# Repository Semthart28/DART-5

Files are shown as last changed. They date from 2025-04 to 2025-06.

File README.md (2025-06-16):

# Upgrading DART: Adding Traffic Light Detection and Control

<p align="center">
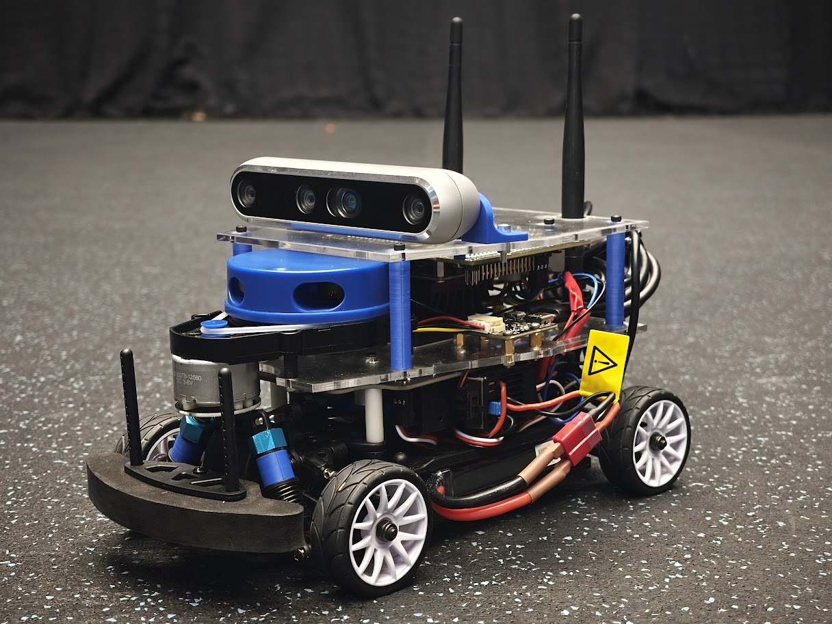
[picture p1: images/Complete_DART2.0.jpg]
  
</p>

# This Repo
In this repository, we're upgrading the DART robot for traffic light detection. DART is a robot, created at the TU Delft, and instructions for building your own DART can be found [here](https://github.com/Lorenzo-Lyons/DART). In this repository, you'll find:
+ <b>Build instructions</b> for physical changes we made.
+ <b>Build instructions</b> for our 3D-printed traffic light.
+ <b>Software for Traffic Light Detection</b> in order that the DART recognises a traffic light and which light it's currently displaying.
+ <b>Control</b> a control algorithm that makes sure the DART stops for a red light, continues through a green light, and acts appropriately to a yellow light.

# Physical Changes We Made to DART
The physical changes we made to the DART:
+ We changed the baseboard and upperboard to lower the center of mass as much as possible, mount the electronics better, and be able to install the new camera setup and LiDar power supply.
+ We connected the LiDAR's power supply directly to the Jetson Nano Expansion Board rather than to the Jetson Nano itself. This setup resolves the issue of the LiDAR drawing too much current from the Jetson Nano.
+ We added a new camera setup to enable the DART to perform traffic light detection.
+ We 3D-printed spacers to stiffen the suspension. (Originally, brass spacers were installed.)

To see the full Build Instructions for these changes, and how to replicate our 3D-printed traffic light, go to [Build Instruction Section](https://github.com/Semthart28/DART-5/tree/main/Build%20Instructions).

# Software for Traffic Light Detection
For the traffic light detection, we trained the YOLOv3-tiny model on roughly 500 images of our 3D-printed traffic light. [YOLO](https://pjreddie.com/darknet/yolo/) 'You Only Look Once' is  an open-source, state-of-the-art real-time object detection system [1]. A short clip of the detection of a traffic light is shown below:

<p align="center">
  Demo of feature
</p>

We drew the bounding boxes around the traffic light with [LabelImg](https://github.com/HumanSignal/labelImg) to create the .txt files that tell the model which class it is (0, 1, or 2 for Red, Yellow, or Green, respectively) and the coordinates that define the bounding box around the traffic light. We then used an 80/20 training/testing split with the images.

Our configuration file is based on [Berktepebag's Github](https://github.com/berktepebag/Traffic-light-detection-with-YOLOv3-BOSCH-traffic-light-dataset) with these changed settings for the training:
+ We set the max iterations to 6000 
+ We set the batch to 64
+ We set the subdivision to 12
+ We set the steps to 4800, 5400

The DART can detect the traffic light colors from more than 1.5 meters away. Below are the instructions to add the traffic light detection to your DART.

### Step 0: Setting up the camera
To set up the camera on the Jetson Nano, run this command:
```
sudo apt-get install ros-$ROS_DISTRO-realsense2-camera
```

### Step 1: Installing Darknet
Darknet from the [original website](https://pjreddie.com/darknet/) is pretty outdated. However, so is the Jetson Nano, so it'll work fine. If you're on your laptop and trying yolo, we recommend installing Darknet via [AlexeyAB's Github](https://github.com/AlexeyAB/darknet), because you're going to run into compatibility issues. But on the Jetson Nano, you should install it from the original website like this:
```
git clone https://github.com/pjreddie/darknet.git
cd darknet
make
```
Now, make sure you've downloaded CUDA and OpenCV. The Jetson Nano already has CUDA pre-installed if you downloaded the Jetpack SDK. In the Makefile in the Darknet directory, edit the lines at the top like this:
```
GPU=1
OPENCV=1
```
Remake Darknet and you're done.

### Step 2: Download our Trained Model
In your Darknet directory, make a folder called 'Model' and add the three files from [this folder](https://github.com/Semthart28/DART-5/tree/main/YOLO-model). Then, make a folder called 'backup' within the 'Model' folder and add the 'yolov3-tiny-tf_best.weights' file in there.

### Step 3: Running the model
Make sure you're in the darknet directory and run this command to run the model:
```
./darknet detector demo Model/tf-data.data Model/yolov3-tiny-tf.cfg Model/backup/yolov3-tiny-tf_best.weights
```
A tab of your camera should now open, and the algorithm will detect traffic lights!

Additionally, you can play around with the threshold of when it will show the traffic light. Just add this at the end of the previous command:

```
-thresh 0.20
```

Now, it detects all traffic lights if the confidence is higher than 20%.

# Control Algorithm 
The first thing we need to do now is to turn our detection algorithm into a ROS package so the DART can act upon this information. This is done via the [darknet_ros Github](https://github.com/leggedrobotics/darknet_ros). Follow the melodic-and-noetic branch, but download the YoloObjectDetector.cpp file from this repository. We made the .cpp file compatible with the DART by using the fix/memory_leak branch. Originally, the RAM would fill up, and the system would freeze. Additionally, we made sure the color codes of Darknet ROS and the Intel camera match up. 

Next up, download the tf_controller_pkg folder from this repository, and put it in your catkin workspace. Remake your catkin workspace and run it with this command:

```
roslaunch tf_controller_pkg tf_controller.launch
```

The safety value is still on, so you have to run the gamepad basic file and hold R1 on the controller to remove the safety value. Comment out all the throttle commands in the gamepad_basic.py file from [Lorenzo's GitHub](https://github.com/Lorenzo-Lyons/DART), and put the throttle value in the racecar_universal.py file to 0.13. Run these in separate terminals:

```
rosrun racecar_pkg racecar_universal.py
```

```
rosrun racecar_pkg gamepad_basic.py
```

Now hold the R1 button on the controller to disable the safety value and the control works!

# References
https://github.com/Lorenzo-Lyons/DART

https://pjreddie.com/darknet/yolo/

https://github.com/berktepebag/Traffic-light-detection-with-YOLOv3-BOSCH-traffic-light-dataset

https://github.com/HumanSignal/labelImg

https://github.com/AlexeyAB/darknet

https://github.com/leggedrobotics/darknet_ros

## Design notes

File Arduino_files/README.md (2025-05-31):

# Arduino Traffic light file
You'll find the Arduino code to power the traffic light and control its lights here. You can change the duration, brightness and order of the lights in this file as you like. For example, during testing you can comment out the code that displays the green and orange light to test whether the DART stops for red.

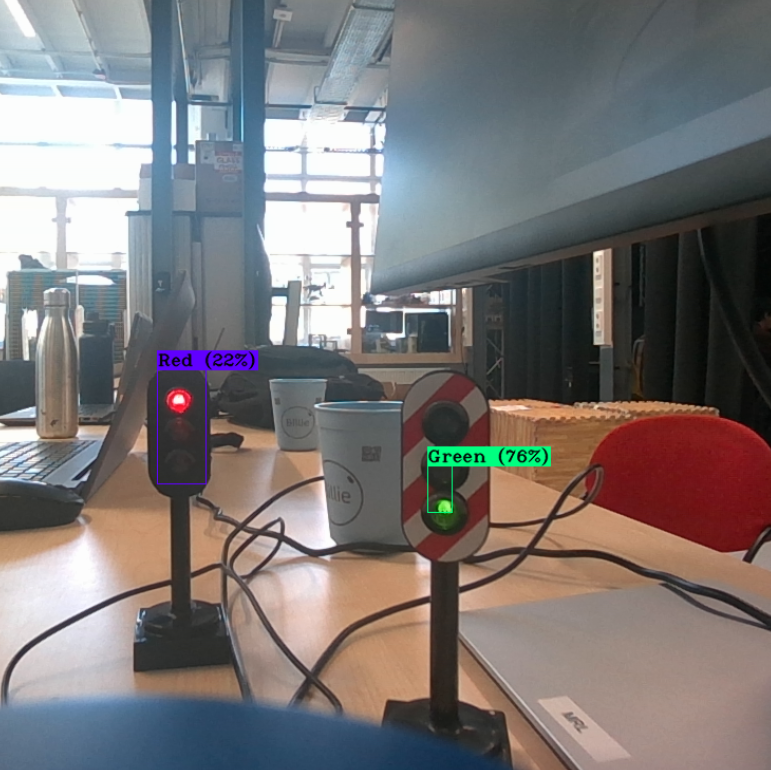
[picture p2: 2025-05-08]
images/Detection.png

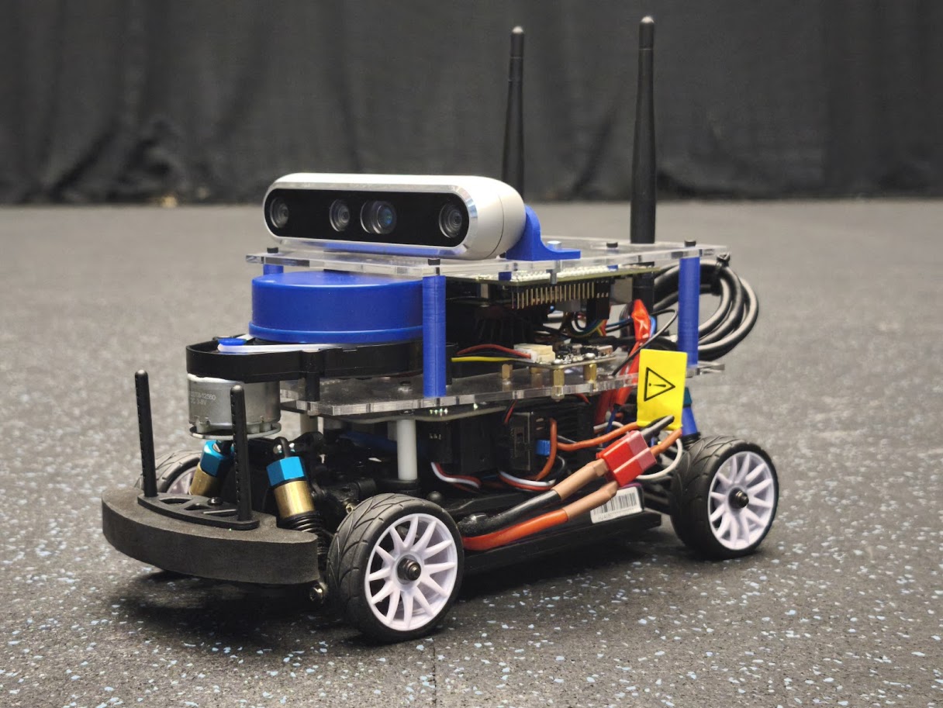
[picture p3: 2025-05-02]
images/Complete_DART.jpg

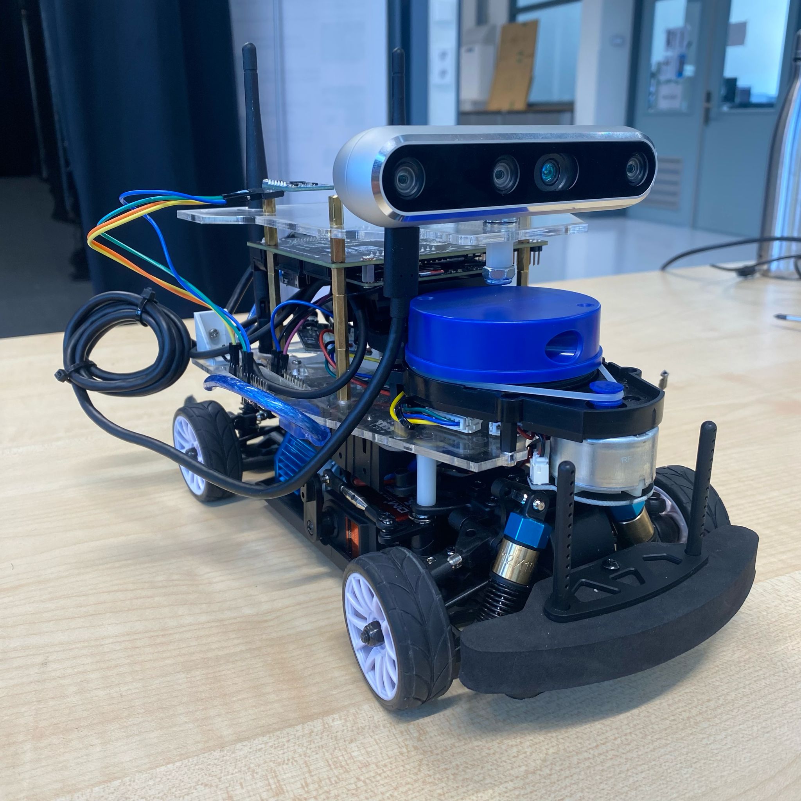
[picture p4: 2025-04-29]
images/DART.jpg

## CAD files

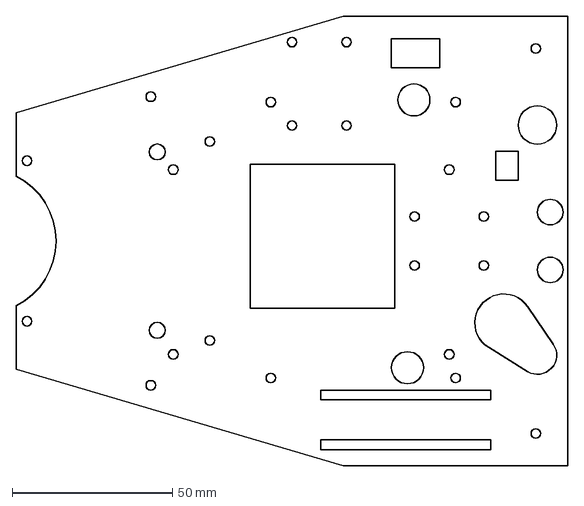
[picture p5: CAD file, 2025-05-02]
Build Instructions/DXF files/PMMA_3mm_1x_baseboard.DXF
172.0 x 140.0 mm

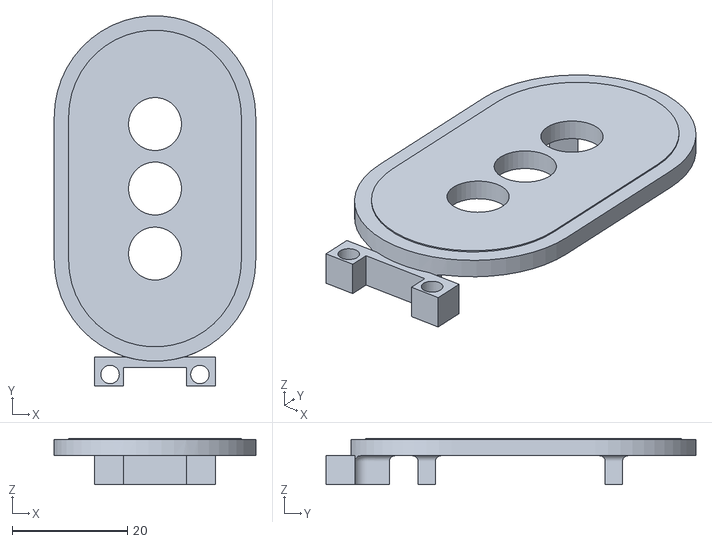
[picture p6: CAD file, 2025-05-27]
Build Instructions/STL files/Traffic light front.STL
35.0 x 64.3 x 8.00

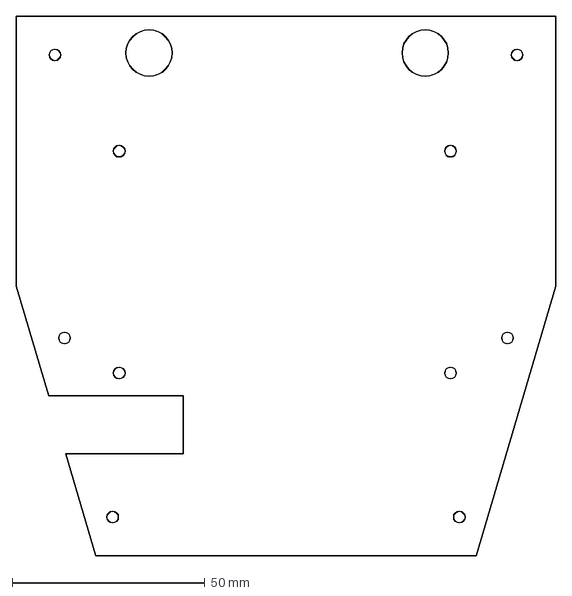
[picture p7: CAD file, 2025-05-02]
Build Instructions/DXF files/PMMA_3mm_1x_topboard.DXF
140.0 x 140.0 mm

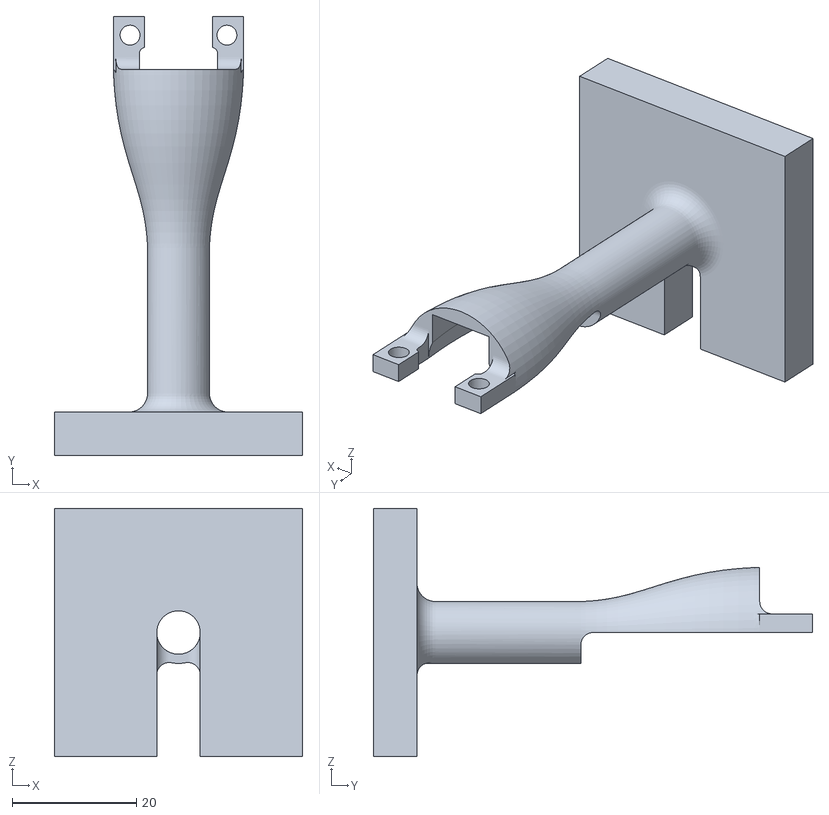
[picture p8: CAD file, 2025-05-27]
Build Instructions/STL files/Traffic light pole.STL
40.0 x 70.7 x 40.0

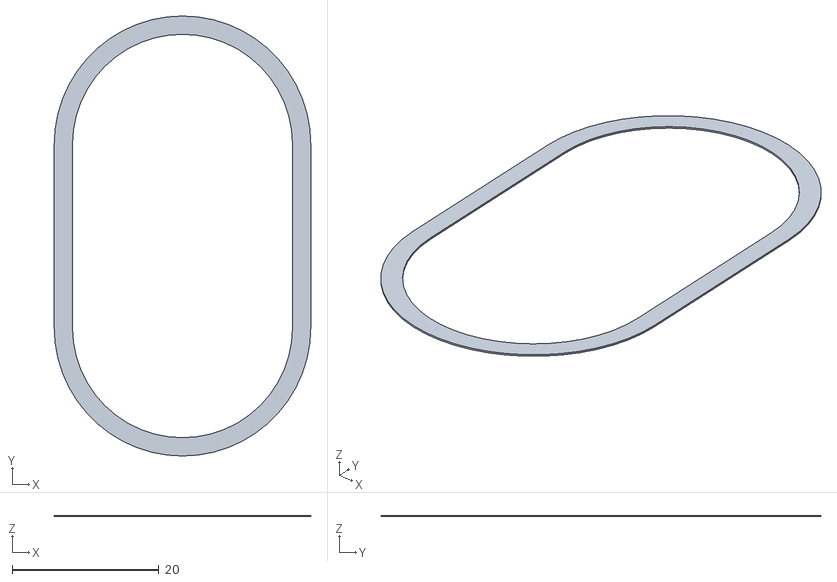
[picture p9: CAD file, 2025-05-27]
Build Instructions/STL files/Traffic light white outer line.STL
35.0 x 60.0 x 0.2

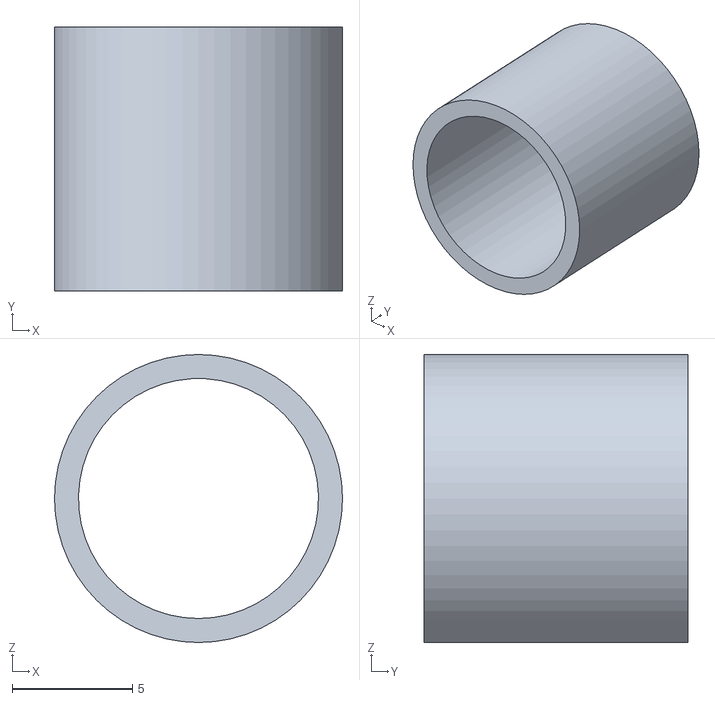
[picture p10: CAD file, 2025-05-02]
Build Instructions/STL files/Bus 12x11.STL
12.0 x 11.0 x 12.0

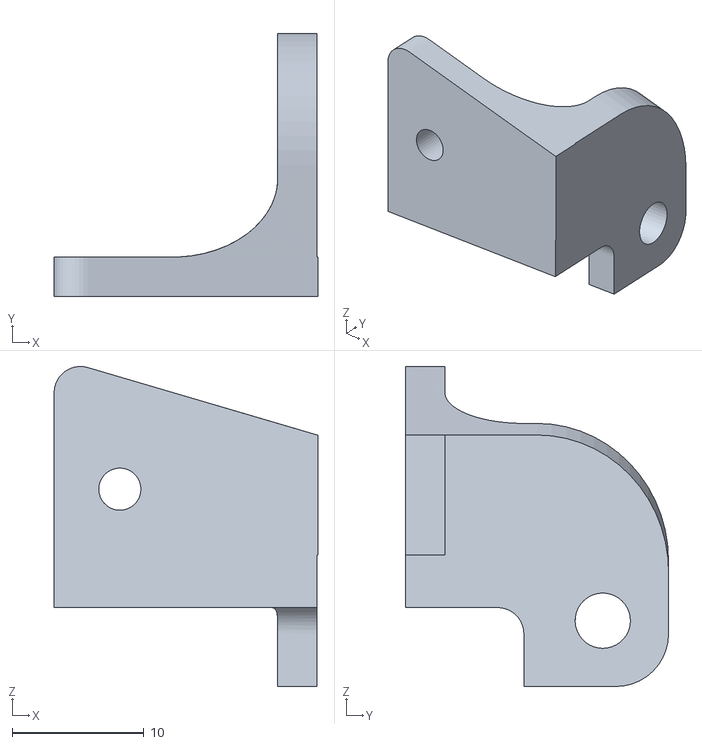
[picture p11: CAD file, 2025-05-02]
Build Instructions/STL files/Intel M4 Camera mount right linked.STL
20.1 x 20.0 x 24.3

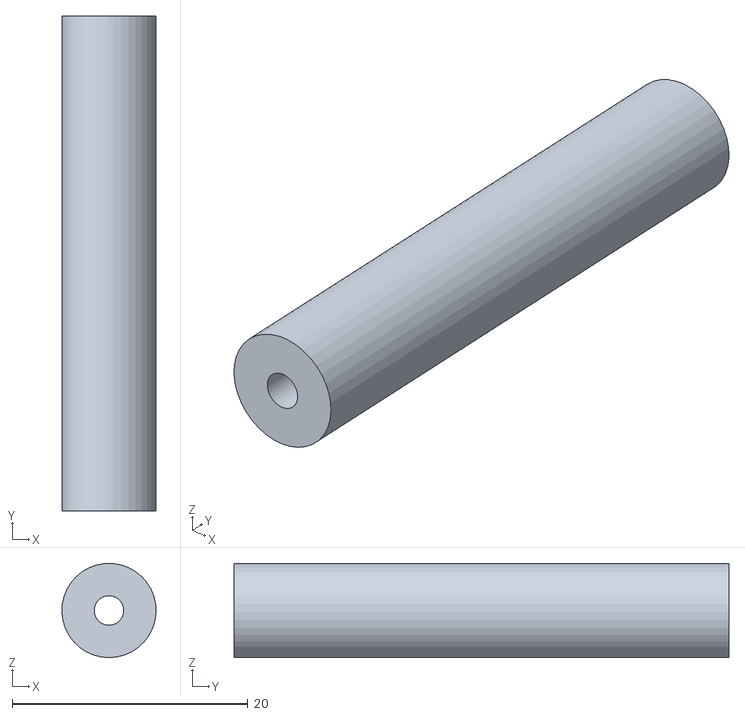
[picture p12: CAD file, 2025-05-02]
Build Instructions/STL files/Standoff 42mm M2.5.STL
7.99 x 42.0 x 8.00

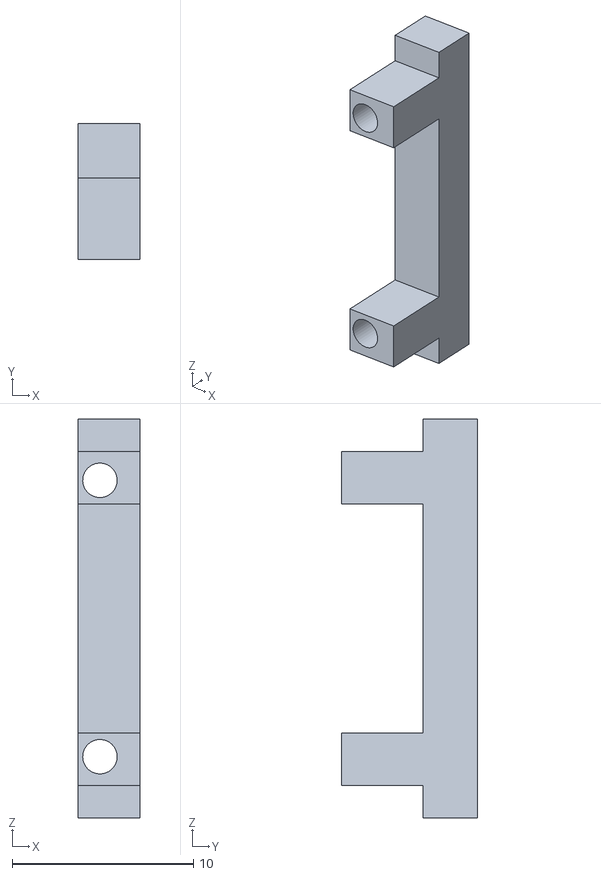
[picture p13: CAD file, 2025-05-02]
Build Instructions/STL files/arduino nano mounts v2.STL
3.40 x 7.50 x 22.0

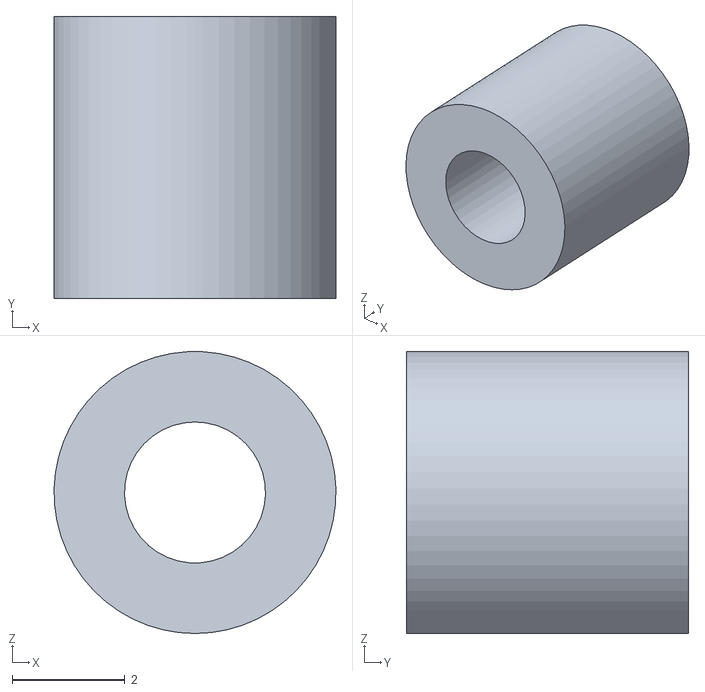
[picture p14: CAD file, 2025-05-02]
Build Instructions/STL files/Standoff 5mm M2.5.STL
5.00 x 5.00 x 5.00

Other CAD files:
Build Instructions/STL files/Intel M4 Camera mount left.STL

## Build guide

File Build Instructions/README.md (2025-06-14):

# Build Instructions
These build instructions assume you already have a DART, according to [Lorenzo Lyon's Github](https://github.com/Lorenzo-Lyons/DART), and want to upgrade it with a camera that's suitable for object detection applications. 

For all applications of DART, even if you don't want to upgrade the camera, it's best practice to follow the rest of the building instructions in this repository. Changing the LiDar's power supply will prevent the Jetson Nano from overheating. Changing the upperboard and baseboard with the 3D-printed standoffs will lower the center of mass as much as possible. The DART is a really fast robot and could tilt easily around a sharp corner. Especially now with a heavy camera on it. So, lowering the center of mass is preferred. Additionally, the Arduino, IMU, and USB Adapter Board for the LiDar can now be mounted to the baseboard.

At the bottom, you can find how we built our 3D-printed traffic light.

# Required Extra Components
+ a micro USB cable for the LiDAR's power supply
+ The updated baseboard and upperboard [dxf files](https://github.com/Semthart28/DART-5/tree/main/Build%20Instructions/DXF%20files)
+ The Intel RealSense Depth Camera D455 [link](https://store.intelrealsense.com/buy-intel-realsense-depth-camera-d455.html)
+ The new 3D-printed parts [STL files](https://github.com/Semthart28/DART-5/tree/main/Build%20Instructions/STL%20files) (Carefully read how many times you need to print each file)
+ Some bolts and screws:
    + 12x M2.5 8mm Stainless Steel Screws
    + 16x M2.5 Stainless Steel Nuts
    + 8x M2.5 6mm-6mm brass female-male
    + 12x M2.5 ~14mm screws
    + 2x M4 ~8mm screws (Intel camera mounts)
    + 2x M3 ~10mm screws
    + 2x M3 nuts
    + 4x M1.6 ~10mm screws 
    + 4x M1.6 nuts
+ This small Arduino LED display for the traffic light [link](https://nl.aliexpress.com/item/1005006161998547.html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)
+ Any Arduino-compatible microcontroller to power and control the timing of the lights of the traffic light

# Changing the LiDar's power supply
In order to change the LiDar's power supply, you need to strip a micro-USB cable. Attach the micro-USB port to the USB adapter board of the LiDAR and solder the stripped end of the cable directly onto the JetRacer Pro Expansionboard as shown in the image below:

<p align="center">
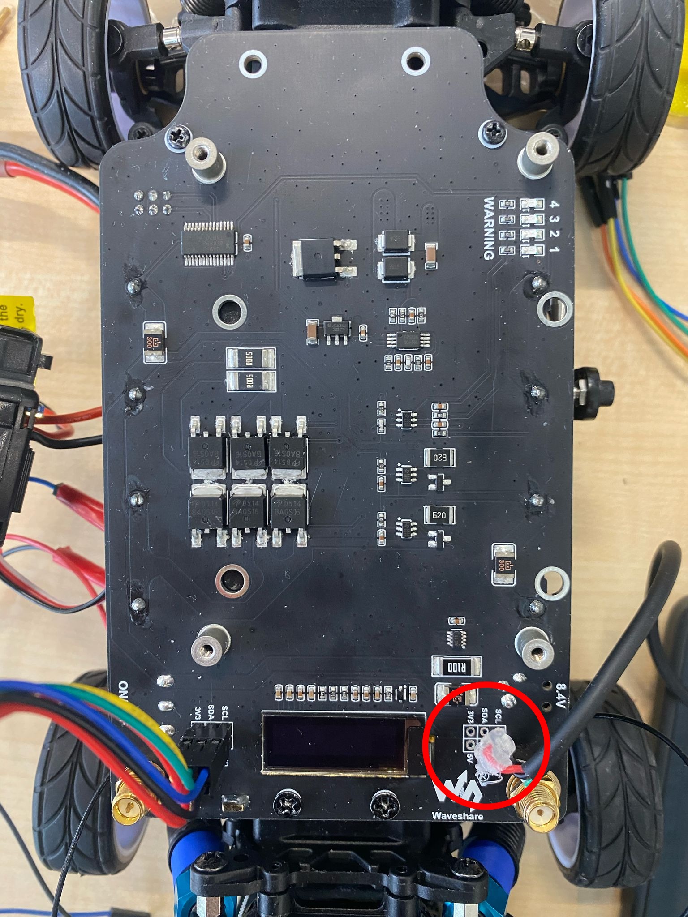
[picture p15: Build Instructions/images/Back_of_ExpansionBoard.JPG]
  
</p>

Solder the red cable of the micro-USB to the labeled '5V' and the black cable to the labeled 'GND' on the right-hand side of the display. Now the LiDar is directly connected to the battery pack.

# Replacing the Baseboard
On the new baseboard, you can attach the IMU and the USB Adapterboard of the LiDar as shown in this image below (left):

<p align="center">
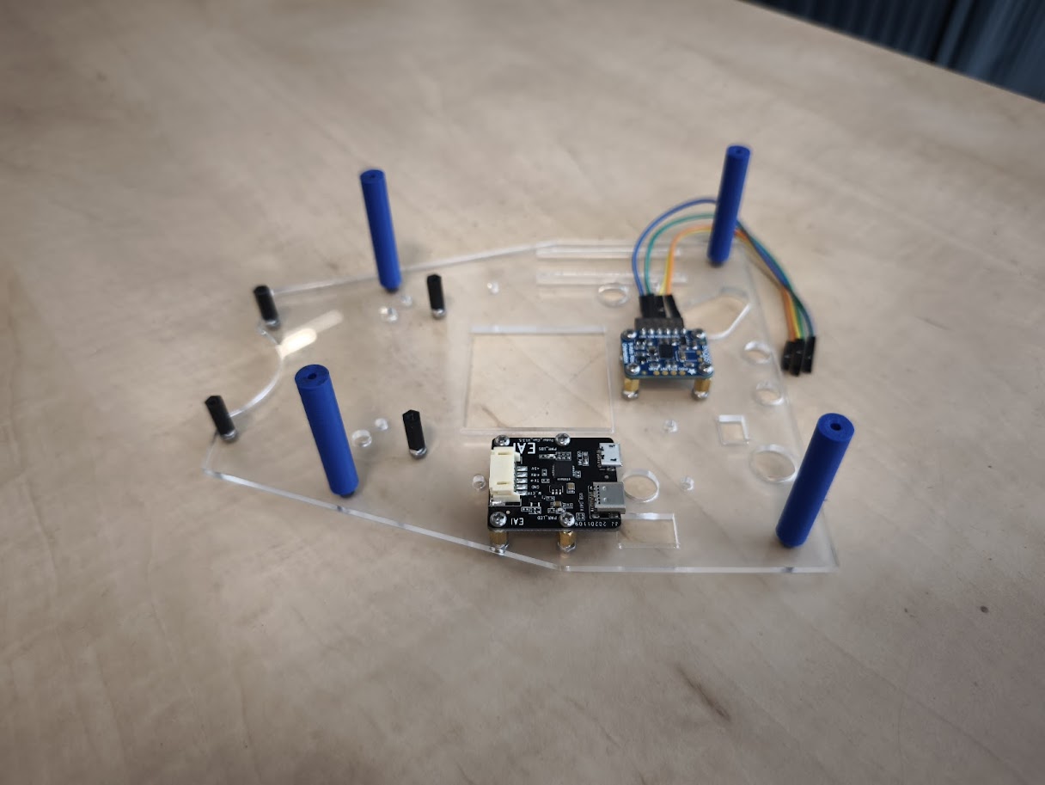
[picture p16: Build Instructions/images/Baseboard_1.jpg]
  
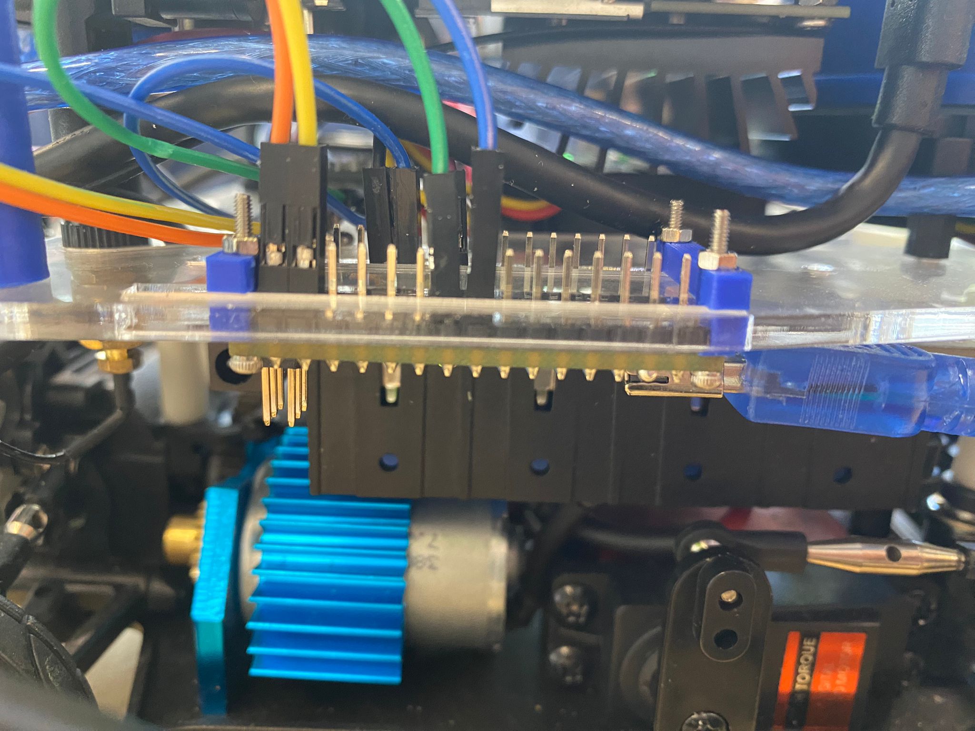
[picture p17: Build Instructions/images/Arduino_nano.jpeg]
  
</p>

On the right, you can see how to attach the Arduino Nano to the slots on the baseboard with the 3D printed pieces.

Attach the blue standoffs and the black standoffs that belong to the LiDar's setup, and then attach the baseboard onto the expansion board.

# Adding the new camera setup
A side-view of the DART is shown below:

<p align="center">
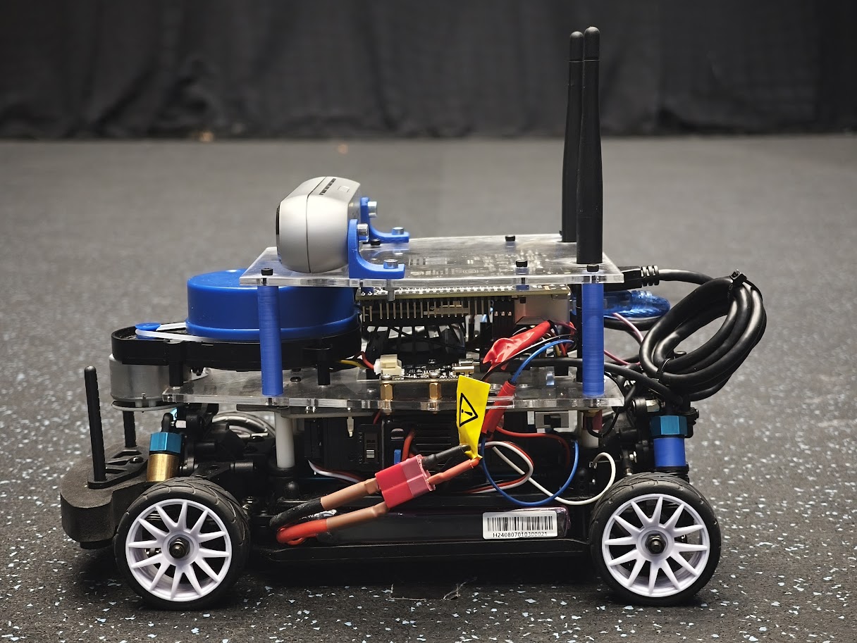
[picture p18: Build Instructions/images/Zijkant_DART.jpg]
  
</p>

Attach the 3D-printed camera mounts to the back of the camera with M4 bolts and to the upperboard with M3 bolts. Plug the USB cable into the Jetson Nano, and your camera setup is done!

# Replacing the Brass spacers of the suspension with 3D-printed spacers (Optional)
If you want to, you can replace the brass spacers of the suspension with the 3D printed 'Bus' STL file.  We did this so we didn't have to buy the brass rings and can print them easily with the other 3D parts.

# 3D-printed traffic light
We designed a small 3D-printed traffic light that resembles a realistic Dutch traffic light. You will need the three 'traffic light' STL files, the LED Arduino display, any Arduino-compatible microcontroller, and the [Arduino code](https://github.com/Semthart28/DART-5/tree/main/Arduino_files).

For printing the white edge of the traffic light, we made a separate 3D model for the white edge, which we merged in the slicer software with the rest. By having two separate STLs, you can assign different colors to the different parts of the traffic light:
<p align="center">
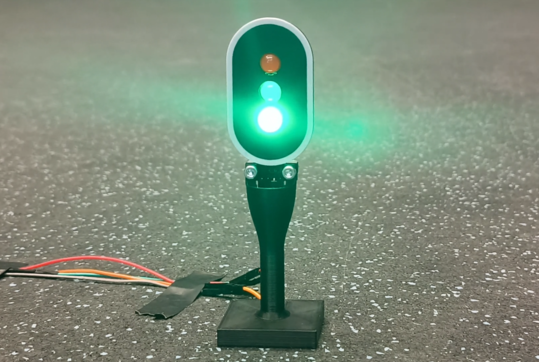
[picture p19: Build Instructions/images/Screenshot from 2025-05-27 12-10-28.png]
  
</p>

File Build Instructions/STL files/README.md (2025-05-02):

# 3D-printed STL Files
All new 3D-printed files are in this folder.
# Amount of each STL File you need to print
+ 'Bus 12x11.stl' 4x
+ 'Intel M4 Camera mount left.STL' 1x
+ 'Intel M4 Camera mount right linked.STL' 1x
+ 'Standoff 42mm M2.5.STL' 4x
+ 'Standoff 5mm M2.5.STL' 4x
+ 'arduino nano mounts v2.STL' 2x

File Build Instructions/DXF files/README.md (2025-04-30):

# DXF Files

This folder contains the two updated lasercut files. Lorenzo probably also updated the baseboard file in his repository, so you might not have to update the baseboard.

Both parts are PMMA and 3mm thick.

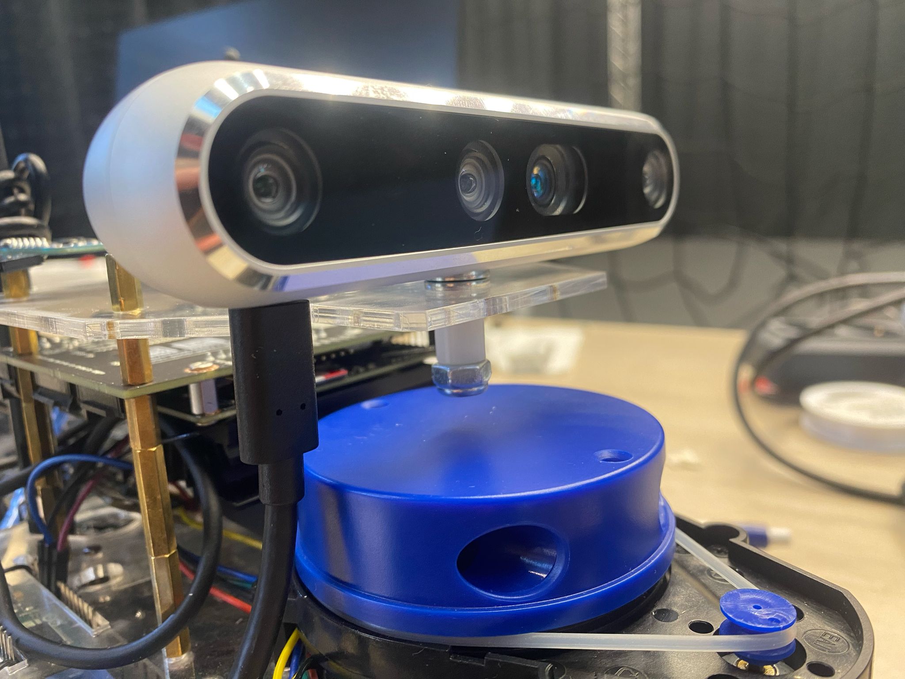
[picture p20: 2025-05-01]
Build Instructions/images/camera-setup.jpg

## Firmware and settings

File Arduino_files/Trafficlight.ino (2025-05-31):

/ PWM Traffic Light Example
const int redPin    = 9;   // must be PWM pin
const int yellowPin = 10;  // must be PWM pin
const int greenPin  = 11;  // must be PWM pin

void setup() {
  pinMode(redPin,    OUTPUT);
  pinMode(yellowPin, OUTPUT);
  pinMode(greenPin,  OUTPUT);
}

void loop() {
  // Turn red on at 100% brightness for 5 s
  analogWrite(redPin, 255);
  delay(5000);
  analogWrite(redPin, 0);

  // Turn green on at 100% brightness for 5 s
  analogWrite(greenPin, 255);
  delay(5000);
  analogWrite(greenPin, 0);

  // Turn yellow on at 100% brightness for 2 s
  analogWrite(yellowPin, 255);
  delay(2000);
  analogWrite(yellowPin, 0);
}

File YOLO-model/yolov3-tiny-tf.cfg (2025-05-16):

[net]
# Testing
# batch=1
# subdivisions=1
Training
batch=64
subdivisions=12
width=416
height=416
channels=3
momentum=0.9
decay=0.0005
angle=0
saturation = 1.5
exposure = 1.5
hue=.1

learning_rate=0.001
burn_in=1000
max_batches = 6000
policy=steps
steps=4800,5400
scales=.1,.1

[convolutional]
batch_normalize=1
filters=16
size=3
stride=1
pad=1
activation=leaky

[maxpool]
size=2
stride=2

[convolutional]
batch_normalize=1
filters=32
size=3
stride=1
pad=1
activation=leaky

[maxpool]
size=2
stride=2

[convolutional]
batch_normalize=1
filters=64
size=3
stride=1
pad=1
activation=leaky

[maxpool]
size=2
stride=2

[convolutional]
batch_normalize=1
filters=128
size=3
stride=1
pad=1
activation=leaky

[maxpool]
size=2
stride=2

[convolutional]
batch_normalize=1
filters=256
size=3
stride=1
pad=1
activation=leaky

[maxpool]
size=2
stride=2

[convolutional]
batch_normalize=1
filters=512
size=3
stride=1
pad=1
activation=leaky

[maxpool]
size=2
stride=1

[convolutional]
batch_normalize=1
filters=1024
size=3
stride=1
pad=1
activation=leaky

###########

[convolutional]
batch_normalize=1
filters=256
size=1
stride=1
pad=1
activation=leaky

[convolutional]
batch_normalize=1
filters=512
size=3
stride=1
pad=1
activation=leaky

[convolutional]
size=1
stride=1
pad=1
filters=24
activation=linear



[yolo]
mask = 3,4,5
anchors = 10,14,  23,27,  37,58,  81,82,  135,169,  344,319
classes=3
num=6
jitter=.3
ignore_thresh = .7
truth_thresh = 1
random=1

[route]
layers = -4

[convolutional]
batch_normalize=1
filters=128
size=1
stride=1
pad=1
activation=leaky

[upsample]
stride=2

[route]
layers = -1, 8

[convolutional]
batch_normalize=1
filters=256
size=3
stride=1
pad=1
activation=leaky

[convolutional]
size=1
stride=1
pad=1
filters=24
activation=linear

[yolo]
mask = 0,1,2
anchors = 10,14,  23,27,  37,58,  81,82,  135,169,  344,319
classes=3
num=6
jitter=.3
ignore_thresh = .7
truth_thresh = 1
random=1
